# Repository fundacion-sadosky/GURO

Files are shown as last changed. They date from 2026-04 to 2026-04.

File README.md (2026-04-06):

🌐 [English](README.en.md)

# GURO

**Kit de conversión para robots Robobloq Qoopers con [BBC Micro:bit](https://www.microbit.org)**

La Fundación Sadosky desarrolla el kit GURO para actualizar los robots Robobloq Qoopers —ya desplegados en escuelas de todo el país— reemplazando el controlador propietario Qmind Plus por la [BBC Micro:bit](https://www.microbit.org): una placa didáctica de hardware y software completamente abiertos, con una comunidad global activa de millones de docentes y estudiantes.

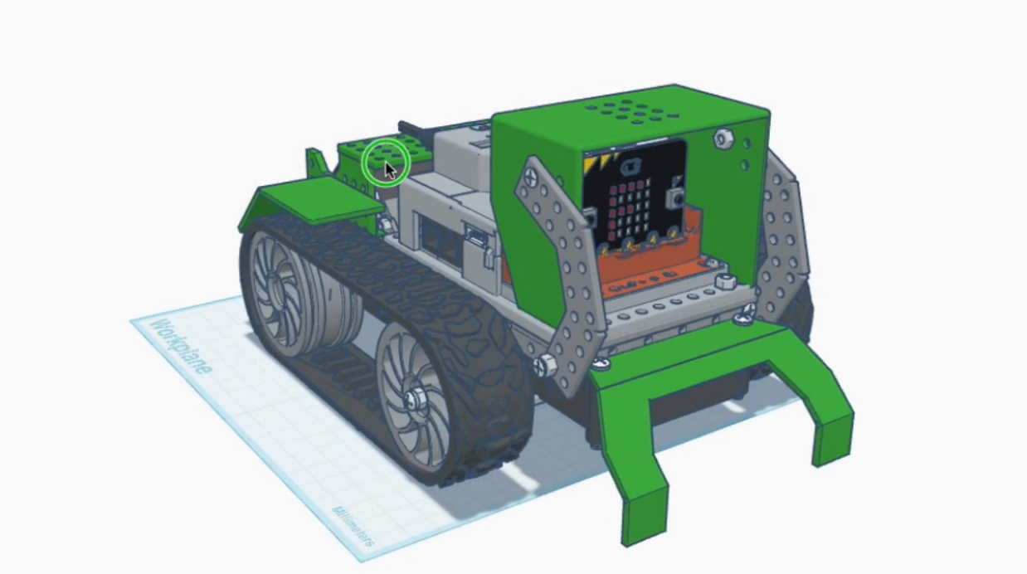
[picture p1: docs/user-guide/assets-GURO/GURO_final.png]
GURO terminado


---

## ¿Qué es el kit GURO?

El kit GURO consiste en una **placa adaptadora** (diseño KiCad incluido en este repositorio) y un **gabinete** que permiten montar una BBC Micro:bit y una placa expansora [Kittenbot Robotbit](https://kittenbothk-eng.readthedocs.io/en/latest/Microbit_eboard/Robotbit/robotbitMC.html) en el chasis del Robobloq Qoopers, conectando los motores y sensores existentes del robot.

El resultado es un robot funcional, programable desde el navegador en bloques visuales o en Python, sin depender de ningún software propietario ni de un único proveedor.

El modelos 3D del robot y el gabinete están disponibles en este repositorio y en [Tinkercad](https://www.tinkercad.com/things/2tzfirybpMV-guro-microrbit-para-robolboq-qoopers-260401)

---

## Requisitos

- **Kit Robobloq Qoopers** — chasis, motores, sensores y partes mecánicas (sin el Qmind Plus)
- **Kit GURO** — placa adaptadora y gabinete Micro:bit (este repositorio)
- **[BBC Micro:bit](https://www.microbit.org)** v1 o v2
- Un destornillador Phillips
- Una computadora con puerto USB

---

## Guía de armado

La documentación completa está publicada en:

**[guro.readthedocs.io](https://guro.readthedocs.io/)**

Incluye el inventario de piezas, 16 pasos ilustrados y las instrucciones de programación. También disponible [en PDF](docs/user-guide_2026-04-01.pdf)

---

## Programación del robot

Una vez armado el GURO, cargá un programa a la Micro:bit desde el navegador, sin instalar nada:

### Opción 1 — Bloques visuales (MakeCode)

Usá el editor [Microsoft MakeCode](https://makecode.microbit.org) con la extensión **Kittenbot Robotbit** para programar el robot con bloques. [Ver instrucciones de la extensión.](https://kittenbothk-eng.readthedocs.io/en/latest/Microbit_eboard/Robotbit/robotbitMC.html)

### Opción 2 — Python

Usá el [editor oficial de MicroPython](https://python.microbit.org/v/3) de la [Micro:bit Educational Foundation](https://github.com/microbit-foundation).

El framework [**microbitML**](https://github.com/fundacion-sadosky/microbitML) (Fundación Sadosky) incluye la actividad `mbGURO`, lista para comandar al robot. Podés descargar el archivo `.hex` y bajarlo directamente a la placa.

---

## Estructura del repositorio

```
docs/               Documentación del sitio (properDocs + Obsidian)
kit GURO/           Inventario del kit 
gabinete/           Gabinete para Micro:bit y placa expansora
placa adaptadora/   Diseño de la placa PCB adaptadora (KiCad)
scripts/            Scripts de generación de documentación (properDocs/MkDocs)
mkdocs.yml          Configuración del sitio de documentación 
docs-requirements.txt  Dependencias Python para compilar la documentación 
```

La carpeta `docs/` está configurada como un vault de [Obsidian](https://obsidian.md), lo que permite editarla sin usar la terminal. Ver [Contribuciones para redactores](https://guro.readthedocs.io/contributing/for-writers/).

---

## Oportunidades de colaboración

Estas son algunas tareas concretas en las que podés contribuir al proyecto:

1. **Avistaje**: si lo usan en tu escuela, compartí la experiencia B)
1. **Completar la Mecánica**: pasar el diseño 3D del gabinete de [Tinkercad](https://www.tinkercad.com/things/2tzfirybpMV-guro-microrbit-para-robolboq-qoopers-260401) a un formato mantenible/paramétrico como openScad.
1. **Completar la Mecánica**: el capó no encaja en la tapa del gabinete.
1. **Completar la Mecánica**: la tapa del gabinete choca con el porta batería del Kittenbot.
1. **Completar la Guía**: los pasos 13, 14 y 16 de la guía de armado no tienen imágenes aún. Si tenés un kit armado, podés tomar las fotos y abrir un PR.
1. **Traducir la documentación al Inglés**: la guía de armado y el README están disponibles solo en español. Traducirlos ampliaría el alcance del proyecto a la comunidad internacional de Micro:bit.
1. **Crear una extensión de MakeCode específica para GURO**: actualmente se usa la extensión genérica de Kittenbot Robotbit. Una extensión propia simplificaría la programación en bloques con nombres y funciones adaptados al GURO.

## Contribuciones

Las contribuciones son bienvenidas, independientemente del perfil técnico.

- **Redactores y docentes**: editá la documentación con [Obsidian](https://obsidian.md) abriendo la carpeta `docs/` como vault. Ver [guía para redactores](https://guro.readthedocs.io/contributing/for-writers/).
- **Desarrolladores**: mirá la [guía para desarrolladores](https://guro.readthedocs.io/contributing/for-developers/).
- **Errores o sugerencias**: abrí un [issue](../../issues) en este repositorio.

---

## Créditos

Colaboradores/as iniciales, por orden alfabético:

| Nombre | Rol |
|---|---|
| Alarcón Lasagno, Ramiro | Doc, SW, HW | 
| Batlle, Leandro | Doc, SW , HW, idea original |
| Gentile Montes, Ezequiel  | Mecánica |
| Medel, Ricardo | Licencias Doc, FLOSS, OSHW  |

*¿Contribuiste al proyecto? Abrí un PR para agregar tu nombre y aportes.*

Este proyecto utiliza la [BBC Micro:bit](https://www.microbit.org), desarrollada por la [Micro:bit Educational Foundation](https://github.com/microbit-foundation). La Micro:bit Foundation publica sus especificaciones de hardware, firmware y recursos educativos bajo licencias abiertas en [github.com/microbit-foundation](https://github.com/microbit-foundation).

---

## Marcas registradas

Los nombres de productos y marcas mencionados en este repositorio (incluyendo BBC Micro:bit, Robobloq, Qoopers, Kittenbot, Robotbit, Microsoft MakeCode, entre otros) son propiedad de sus respectivos titulares y se utilizan únicamente con fines identificativos y descriptivos.

## Naturaleza del proyecto

El desarrollo comenzó en la Fundación Sadosky en el marco del Programa para el Desarrollo de la Infraestructura destinada a Promover la Capacidad Emprendedora financiado por la [CAF | Banco de desarrollo de América Latina y El Caribe](https://www.caf.com/).  GURO es un kit de conversión que permite reutilizar las partes mecánicas, motores y sensores del Robobloq Qoopers con una nueva  placa controladora. El proyecto no modifica ni redistribuye el firmware, software ni diseños de hardware de los productos de terceros que integra. 

## Garantías y responsabilidad

Este proyecto se distribuye sin garantía de ningún tipo, expresa o  implícita. El armado, uso y eventual modificación del kit son responsabilidad exclusiva del usuario. Consultá las licencias GPLv3 y CC BY-SA 4.0 incluidas en este repositorio para los términos  completos. El uso del kit en entornos educativos debe realizarse bajo supervisión docente y conforme a las normativas de seguridad aplicables en cada jurisdicción. 

## Licencias

El proyecto se distribuye bajo una **licencia dual**:

### Código y diseños de hardware
Publicado bajo la [**GNU General Public License v3.0**](LICENSE) (GPLv3).
Podés usar, modificar y redistribuir el código y los diseños KiCad, siempre que cualquier obra derivada se publique bajo la misma licencia.

### Documentación
Publicada bajo [**Creative Commons Atribución-CompartirIgual 4.0 Internacional**](https://creativecommons.org/licenses/by-sa/4.0/) (CC BY-SA 4.0).
Podés copiar, adaptar y redistribuir el contenido —incluso con fines comerciales— siempre que des crédito a los autores originales y distribuyas las obras derivadas bajo la misma licencia.

---

<p align="center">
  <a href="https://www.fundacionsadosky.org.ar">Fundación Sadosky</a>
</p>

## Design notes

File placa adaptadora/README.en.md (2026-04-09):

🌐 [Español](README.md)

# Adapter Board — GURO Kit

[KiCad](https://www.kicad.org/) design of the **adapter board**, a component of the [GURO kit](../kit%20GURO/README.md).

---

## What does this board do?

The adapter board is the central electrical bridge of the GURO kit.
It connects all the peripherals of the Qoopers chassis to the [Kittenbot Robotbit](https://kittenbothk-eng.readthedocs.io/en/latest/Microbit_eboard/Robotbit/robotbitMC.html):

```
Kittenbot Robotbit
      │
      ├── Motors (×2) — 6-pin connectors
      ├── sensors   ─┐
      ├── GPIO       ├── RJ25 connectors (6 Positions / 6 Contacts)
      └── LED panel ─┘
```

It also handles the connection to the kit's **power board**:

> [!WARNING]
> NEVER connect the Robobloq Qoopers battery directly to the Kittenbot Robotbit: the battery voltage must be regulated down to 5V (at 15W), which is the function of the "power board".

---

## PCB design view

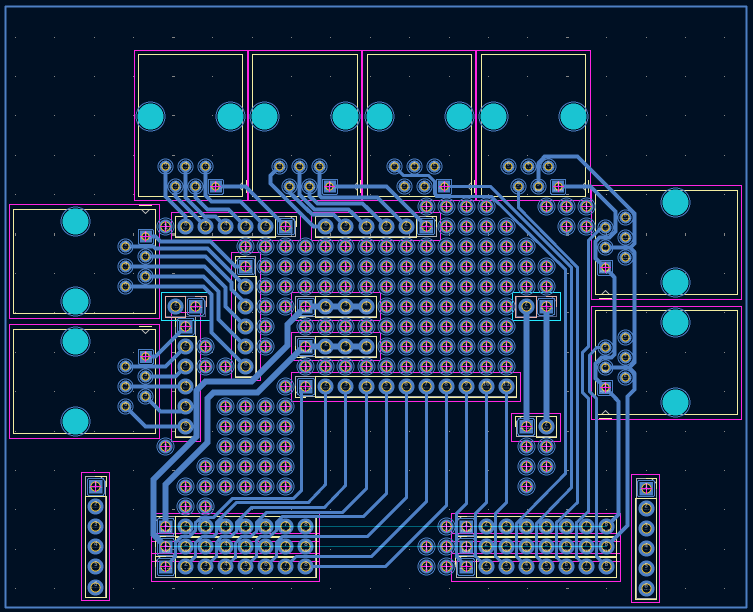
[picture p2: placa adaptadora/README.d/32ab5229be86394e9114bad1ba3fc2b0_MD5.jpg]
KiCad design of the adapter board


The design is optimized to be **interchangeable with a [50×70 mm perfboard](https://www.printables.com/model/797008-perfboard-50x70mm-18-x-24-holes)**, allowing it to be replicated without access to professional PCB manufacturing.

---

## Manufacturing or replacement options

| Option | Difficulty | Result |
|---|---|---|
| **A** — Manufacture from KiCad files | Medium — requires sending Gerbers to a manufacturer | Professional, reproducible PCB |
| **B** — 50×70 mm perfboard | Medium — requires soldering | Equivalent result, no external manufacturer |
| **C** — Direct wiring, no PCB | Low — dupont cables | Functional, less tidy |

All options yield an electrically equivalent result.

---

## Option A — Manufacture from KiCad files

The files in this folder are a [KiCad](https://www.kicad.org/) project (free and open-source PCB design software).

**To manufacture:**
1. Open the project in KiCad and export the **Gerber files** (File → Fabrication Outputs → Gerbers)
2. Upload the Gerbers to any PCB manufacturing service (JLCPCB, PCBWay, Aisler, etc.)
3. Typical order: 5 units, 2 layers, FR4, 1.6 mm thickness

**To edit the design**, you need [KiCad 7 or later](https://www.kicad.org/download/).

---

## Option B — 50×70 mm perfboard

### Components needed for soldering

| Component | Quantity | Notes |
|---|---|---|
| 50×70 mm perfboard | 1 | 2.54 mm pitch |
| Female RJ25 connector (6P6C) | 5 | For sensors and LED panel |
| Male 2-pin connector (2.54 mm pitch) | 2 | For motors |
| Female 40-pin header (2.54 mm pitch) | 2 | For Kittenbot Robotbit |
| Connection wire (wire wrap or similar) | — | For pad bridges |

### General procedure

1. Position the RJ25 connectors using the PCB layout as a reference
2. Solder the connectors and trace the bridges following the KiCad schematic
3. Verify continuity with a multimeter before connecting

---

## Option C — Direct wiring, no PCB

If you have no soldering iron or manufacturer available, it is possible to connect the peripherals directly to the Kittenbot Robotbit using **dupont cables**, without any PCB.

See [step 13 (motors)](../docs/user-guide/index.en.md) and [step 14 (sensors)](../docs/user-guide/index.en.md) of the assembly guide for connection details.

---

## Safety and License

All safety, health, and licensing terms from the [legal section of the main repository](../README.md#guarantees-and-liability) apply here, especially when soldering or handling electrical tools.

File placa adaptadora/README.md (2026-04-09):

🌐 [English](README.en.md)

# Placa Adaptadora — Kit GURO

Diseño [KiCad](https://www.kicad.org/) de la **placa adaptadora**, componente del [kit GURO](../kit%20GURO/README.md).

---

## ¿Qué hace esta placa?

La placa adaptadora es el puente eléctrico central del kit GURO.
Conecta todos los periféricos del chasis Qoopers a la [Kittenbot Robotbit](https://kittenbothk-eng.readthedocs.io/en/latest/Microbit_eboard/Robotbit/robotbitMC.html):

```
Kittenbot Robotbit
      │
      ├── Motores (×2) — conectores de 6 pines
      ├── Sensores  ─┐
      ├── GPIO       ├── conectores RJ25 (6 Posiciones / 6 Contactos)
      └── Panel LED ─┘
```

También incorpora la conexión a la **placa de alimentación** del kit, PRECAUCIÓN:

> [!WARNING]
> NUNCA conectar la batería del Robobloq Qoopers directamente al Kittenbot Robotbit: es necesario regular su tensión a 5V (con 15W), que es la función de la "placa de alimentación".

---

## Vista del diseño PCB

Diseño KiCad de la placa adaptadora

El diseño está optimizado para ser **intercambiable con una [placa universal de 50×70 mm](https://www.printables.com/model/797008-perfboard-50x70mm-18-x-24-holes)**, lo que permite replicarla sin acceso a fabricación de PCB profesional.

---

## Opciones de fabricación o reemplazo

| Opción | Dificultad | Resultado |
|---|---|---|
| **A** — Fabricar con los archivos KiCad | Media — requiere enviar Gerbers a un fabricante | PCB profesional, reproducible |
| **B** — Placa universal 50×70 mm | Media — requiere soldadura | Resultado equivalente, sin fabricante externo |
| **C** — Conexión directa sin PCB | Baja — cables y dupont | Funcional, menos prolijo |

Cualquiera sea la opción elegida, el resultado eléctrico es equivalente.

---

## Opción A — Fabricar con los archivos KiCad

Los archivos de esta carpeta son un proyecto de [KiCad](https://www.kicad.org/) (software libre de diseño de PCB).

**Para fabricar:**
1. Abrí el proyecto en KiCad y exportá los **archivos Gerber** (Archivo → Fabricar → Gerbers)
2. Subí los Gerbers a cualquier servicio de fabricación de PCB (JLCPCB, PCBWay, Aisler, etc.)
3. Pedido típico: 5 unidades, 2 capas, FR4, 1.6 mm de espesor

**Para editar el diseño**, necesitás [KiCad 7 o superior](https://www.kicad.org/download/).

---

## Opción B — Placa universal 50×70 mm

### Componentes necesarios para soldar

| Componente | Cantidad | Notas |
|---|---|---|
| Placa universal perforada 50×70 mm | 1 | Paso de 2.54 mm |
| Conector RJ25 hembra (6P6C) | 5 | Para sensores y panel LED |
| Conector 2 pines macho (paso 2.54 mm) | 2 | Para motores |
| Pin header hembra 40 pines (paso 2.54 mm) | 2 | Para Kittenbot Robotbit |
| Cable de conexión (wire wrap o similar) | — | Para puentes entre pads |

### Procedimiento general

1. Posicioná los conectores RJ25 siguiendo el layout del PCB como referencia
2. Soldá los conectores y trazá los puentes según el esquemático KiCad
3. Verificá continuidad con multímetro antes de conectar

---

## Opción C — Conexión directa sin PCB

Si no disponés de soldador ni fabricante, es posible conectar directamente los periféricos a la Kittenbot Robotbit con **cables dupont**, sin PCB intermedio.

Consultá el [paso 13 (motores)](../docs/user-guide/index.md) y el [paso 14 (sensores)](../docs/user-guide/index.md) de la guía de armado para el detalle de cada conexión.

---

## Precauciones y Licencia

Aplican todas las licencias y precauciones de seguridad y salud citadas en el [apartado legal del repositorio principal](../README.md#garantías-y-responsabilidad), especialmente al realizar soldadura y manipulación de herramientas eléctricas.

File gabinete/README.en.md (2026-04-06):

🌐 [Castellano](README.md)

Case
====

The robot model and the case are available in this repository and on [Tinkercad](https://www.tinkercad.com/things/2tzfirybpMV-guro-microrbit-para-robolboq-qoopers-260401).

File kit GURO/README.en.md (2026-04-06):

🌐 [Castellano](README.md)

# GURO Kit

The GURO kit is the set of parts and documents that allow converting a Robobloq Qoopers robot into a robot with fully open hardware and software, replacing the proprietary Qmind Plus controller with a BBC Micro:bit.

The manufacturing files for all kit parts are available in this repository: the adapter board design in the `placa adaptadora/` folder (KiCad) and the case model in the `gabinete/` folder (STL for 3D printing).

---

## Kit inventory

| Part | Qty. | Notes |
|---|---|---|
| case (base) | 1 | 3D printed. STL file in `gabinete/` |
| case (lid) | 1 | 3D printed. STL file in `gabinete/` |
| Adapter board | 1 | PCB designed in KiCad. Files in `placa adaptadora/` |
| Kittenbot Robotbit board | 1 | Commercial PCB for Micro:bit expansion |
| Power board | 1 | Commercial PCB that regulates voltage from the battery |
| Power cable | 1 | Connects the battery to the power board |

You can build your own kit ("DIY" or "maker") anywhere in the world from this repo's documentation:
1. For the adapter board, there are two options:
   2. Manufacture the PCB from the repo design
   3. Start from a prototype (or "universal") 50×70 mm board and solder the tracks and connectors
2. Print the case (base and lid)
2. Obtain the commercial components: Kittenbot Robotbit and the Power Board

---

## Required components (not included in the kit)

The GURO kit must be combined with the following components, obtained separately:

| Component | Notes |
|---|---|
| BBC Micro:bit v1 or v2 | Main controller board |
| Robobloq Qoopers kit | Does not need to be complete — see the assembly guide |

---

## Assembly guide

The complete step-by-step assembly guide is in the `docs/` folder and accessible at:

**[guro.readthedocs.io](https://guro.readthedocs.io/)**

Also available in PDF at `docs/user-guide_2026-04-01.pdf`.

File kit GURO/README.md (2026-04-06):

🌐 [English](README.en.md)

# Kit GURO

El kit GURO es el conjunto de piezas y documentos, que permiten convertir un robot Robobloq Qoopers en un robot de hardware y software completamente abiertos, reemplazando el controlador propietario Qmind Plus por una BBC Micro:bit.

Los archivos de fabricación de todas las piezas del kit están disponibles en este repositorio: el diseño de la placa adaptadora en la carpeta `placa adaptadora/` (KiCad) y el modelo del gabinete en la carpeta `gabinete/` (STL para impresión 3D).

---

## Inventario del kit

| Pieza | Cant. | Notas |
|---|---|---|
| gabinete (base) | 1 | Impresa en 3D. Archivo STL en `gabinete/` |
| gabinete (tapa) | 1 | Impresa en 3D. Archivo STL en `gabinete/` |
| Placa adaptadora | 1 | PCB diseñada en KiCad. Archivos en `placa adaptadora/` |
| Placa Kittenbot Robotbit | 1 | PCB comercial para expansión de la micro:bit | |
| Placa de alimentación | 1 | PCB comercial que regula la tensión desde la batería | |
| Cable de alimentación | 1 | conecta la batería con la placa de alimentación |

Es posible armar tu propio kit ("DIY" o "maker") en cualquier lugar del mundo, a partir de la documentación de este repo:
1. para la placa adaptadora, hay dos opciones:
   2. fabricar el PCB con el diseño del repo
   3. partir de una placa de prototipado (o "universal") de 50x70 mm, y soldar las pistas y conectores
2. imprimiendo el gabinete (base y tapa)
2. consiguendo los componentes comerciales: Kittenbot Robotbit y Placa de Alimentación

---

## Componentes necesarios (no incluidos en el kit)

El kit GURO debe combinarse con los siguientes componentes, que se consiguen por separado:

| Componente | Notas |
|---|---|
| BBC Micro:bit v1 o v2 | Placa controladora principal |
| Kit Robobloq Qoopers | no es necesario que esté completo, ver la Guía de armado|

---

## Guía de armado

La guía completa de armado paso-a-paso está en la carpeta `docs/` y accesible en:

**[guro.readthedocs.io](https://guro.readthedocs.io/)**

También disponible en PDF en `docs/user-guide_2026-04-01.pdf`.

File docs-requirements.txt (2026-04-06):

properdocs
properdocs[i18n]
mkdocs-static-i18n
mkdocs-material[i18n]
mkdocstrings[python]
mkdocs-gen-files
mkdocs-literate-nav
mkdocs-section-index
mkdocs-obsidian-bridge
mkdocs-autorefs
pymdown-extensions

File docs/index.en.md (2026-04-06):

---
title: Home
---

# GURO

**Conversion kit for Robobloq Qoopers robots with [BBC Micro:bit](https://www.microbit.org)**

Fundación Sadosky develops the GURO kit to upgrade Robobloq Qoopers robots — already deployed in schools across the country — by replacing the proprietary Qmind Plus controller with the [BBC Micro:bit](https://www.microbit.org): an educational board with fully open hardware and software, with an active global community of millions of teachers and students.

GURO assembled

---

## What is the GURO kit?

The GURO kit consists of an **adapter board** and a **case** that allow mounting a BBC Micro:bit and a [Kittenbot Robotbit](https://kittenbothk-eng.readthedocs.io/en/latest/Microbit_eboard/Robotbit/robotbitMC.html) expansion board on the Robobloq Qoopers chassis, connecting the robot's existing motors and sensors.

The result is a functional robot, programmable from the browser using visual blocks or Python, without depending on any proprietary software or a single vendor.

The kit designs and the 3D model of the case are available in the [project repository](https://github.com/fundacion-sadosky/GURO) and on [Tinkercad](https://www.tinkercad.com/things/2tzfirybpMV-guro-microrbit-para-robolboq-qoopers-260401).

---

## Quick access

| I want to… | Go to |
|---|---|
| Assemble the robot | [Getting started](getting-started.md) |
| Read the full assembly guide | [User guide](user-guide/index.md) |
| Contribute to the project | [Contributing](contributing/index.md) |
| View source code and designs | [github.com/fundacion-sadosky/GURO](https://github.com/fundacion-sadosky/GURO) |
| Download the adapter board (KiCad) | [placa adaptadora/](https://github.com/fundacion-sadosky/GURO/tree/main/placa%20adaptadora) |
| Download the case (STL) | [gabinete/](https://github.com/fundacion-sadosky/GURO/tree/main/gabinete) |
| Report a bug or suggest an improvement | [Issues](https://github.com/fundacion-sadosky/GURO/issues) |
| Guide in PDF | [user-guide_2026-04-01.pdf](https://github.com/fundacion-sadosky/GURO/raw/main/docs/user-guide_2026-04-01.pdf) |

---

## Requirements

- **Robobloq Qoopers kit** — chassis, motors, sensors and mechanical parts (without the Qmind Plus)
- **[GURO kit](https://github.com/fundacion-sadosky/GURO/tree/main/kit%20GURO)** — the official one or a handmade assembly
- **[BBC Micro:bit](https://www.microbit.org)** v1 or v2
- A Phillips screwdriver
- A computer with a USB port

---

## Programming the robot

Once the GURO is assembled, load a program onto the Micro:bit from the browser, without installing anything:

**Option 1 — Visual blocks:** use [Microsoft MakeCode](https://makecode.microbit.org) with the **Kittenbot Robotbit** extension.

**Option 2 — Python:** use the [official MicroPython editor](https://python.microbit.org/v/3). The [**microbitML**](https://github.com/fundacion-sadosky/microbitML) framework (Fundación Sadosky) includes the `mbGURO` activity, ready to command the robot.

---

## Repository

The entire project is open code and hardware:

- **Main repository:** [github.com/fundacion-sadosky/GURO](https://github.com/fundacion-sadosky/GURO)
- **Adapter board design (KiCad):** [placa adaptadora/](https://github.com/fundacion-sadosky/GURO/tree/main/placa%20adaptadora)
- **3D model of the case (STL):** [gabinete/](https://github.com/fundacion-sadosky/GURO/tree/main/gabinete)
- **Kit inventory:** [kit GURO/](https://github.com/fundacion-sadosky/GURO/tree/main/kit%20GURO)
- **Issues and suggestions:** [github.com/fundacion-sadosky/GURO/issues](https://github.com/fundacion-sadosky/GURO/issues)
- **Contributing:** [CONTRIBUTING.md](https://github.com/fundacion-sadosky/GURO/blob/main/CONTRIBUTING.md)
- **Code of conduct:** [CODE_OF_CONDUCT.md](https://github.com/fundacion-sadosky/GURO/blob/main/CODE_OF_CONDUCT.md)

The project is distributed under a dual license: **GPLv3** for code and hardware designs, **CC BY-SA 4.0** for documentation.

---

<p align="center">
  <a href="https://www.fundacionsadosky.org.ar">Fundación Sadosky</a>
</p>

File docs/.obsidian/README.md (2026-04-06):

🌐 [English](README.en.md)

PLACEHOLDER FILE

éste repositorio permite editar la la documentación con [Obsidian](https://obsidian.md)

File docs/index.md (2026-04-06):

---
title: Inicio
---

# GURO

**Kit de conversión para robots Robobloq Qoopers con [BBC Micro:bit](https://www.microbit.org)**

La Fundación Sadosky desarrolla el kit GURO para actualizar los robots Robobloq Qoopers —ya desplegados en escuelas de todo el país— reemplazando el controlador propietario Qmind Plus por la [BBC Micro:bit](https://www.microbit.org): una placa didáctica de hardware y software completamente abiertos, con una comunidad global activa de millones de docentes y estudiantes.

GURO terminado

---

## ¿Qué es el kit GURO?

El kit GURO consiste en una **placa adaptadora** y un **gabinete** que permiten montar una BBC Micro:bit y una placa expansora [Kittenbot Robotbit](https://kittenbothk-eng.readthedocs.io/en/latest/Microbit_eboard/Robotbit/robotbitMC.html) en el chasis del Robobloq Qoopers, conectando los motores y sensores existentes del robot.

El resultado es un robot funcional, programable desde el navegador en bloques visuales o en Python, sin depender de ningún software propietario ni de un único proveedor.

Los diseños del kit y el modelo 3D del gabinete están disponibles en el [repositorio del proyecto](https://github.com/fundacion-sadosky/GURO) y en [Tinkercad](https://www.tinkercad.com/things/2tzfirybpMV-guro-microrbit-para-robolboq-qoopers-260401).

---

## Accesos rápidos

| Quiero... | Ir a |
|---|---|
| Armar el robot | [Primeros pasos](getting-started.md) |
| Leer la guía completa de armado | [Guía de usuario](user-guide/index.md) |
| Contribuir al proyecto | [Contribuciones](contributing/index.md) |
| Ver el código fuente y los diseños | [github.com/fundacion-sadosky/GURO](https://github.com/fundacion-sadosky/GURO) |
| Descargar la placa adaptadora (KiCad) | [placa adaptadora/](https://github.com/fundacion-sadosky/GURO/tree/main/placa%20adaptadora) |
| Descargar el gabinete (STL) | [gabinete/](https://github.com/fundacion-sadosky/GURO/tree/main/gabinete) |
| Reportar un error o sugerir una mejora | [Issues](https://github.com/fundacion-sadosky/GURO/issues) |
| Guía en PDF | [user-guide_2026-04-01.pdf](https://github.com/fundacion-sadosky/GURO/raw/main/docs/user-guide_2026-04-01.pdf) |

---

## Requisitos

- **Kit Robobloq Qoopers** — chasis, motores, sensores y partes mecánicas (sin el Qmind Plus)
- **[Kit GURO](https://github.com/fundacion-sadosky/GURO/tree/main/kit%20GURO)** — el oficial o un armado artesanalmente 
- **[BBC Micro:bit](https://www.microbit.org)** v1 o v2
- Un destornillador Phillips
- Una computadora con puerto USB

---

## Programación del robot

Una vez armado el GURO, cargá un programa a la Micro:bit desde el navegador, sin instalar nada:

**Opción 1 — Bloques visuales:** usá [Microsoft MakeCode](https://makecode.microbit.org) con la extensión **Kittenbot Robotbit**.

**Opción 2 — Python:** usá el [editor oficial de MicroPython](https://python.microbit.org/v/3). El framework [**microbitML**](https://github.com/fundacion-sadosky/microbitML) (Fundación Sadosky) incluye la actividad `mbGURO`, lista para comandar al robot.

---

## Repositorio

Todo el proyecto es de código y hardware abiertos:

- **Repositorio principal:** [github.com/fundacion-sadosky/GURO](https://github.com/fundacion-sadosky/GURO)
- **Diseño de la placa adaptadora (KiCad):** [placa adaptadora/](https://github.com/fundacion-sadosky/GURO/tree/main/placa%20adaptadora)
- **Modelo 3D del gabinete (STL):** [gabinete/](https://github.com/fundacion-sadosky/GURO/tree/main/gabinete)
- **Inventario del kit:** [kit GURO/](https://github.com/fundacion-sadosky/GURO/tree/main/kit%20GURO)
- **Issues y sugerencias:** [github.com/fundacion-sadosky/GURO/issues](https://github.com/fundacion-sadosky/GURO/issues)
- **Contribuciones:** [CONTRIBUTING.md](https://github.com/fundacion-sadosky/GURO/blob/main/CONTRIBUTING.md)
- **Código de conducta:** [CODE_OF_CONDUCT.md](https://github.com/fundacion-sadosky/GURO/blob/main/CODE_OF_CONDUCT.md)

El proyecto se distribuye bajo licencia dual: **GPLv3** para código y diseños de hardware, **CC BY-SA 4.0** para documentación.

---

<p align="center">
  <a href="https://www.fundacionsadosky.org.ar">Fundación Sadosky</a>
</p>

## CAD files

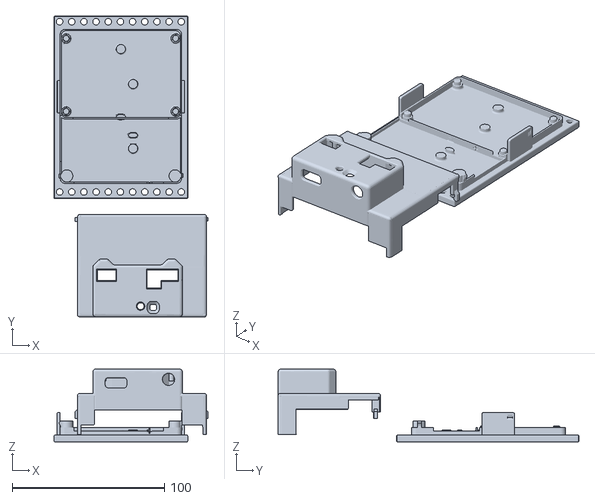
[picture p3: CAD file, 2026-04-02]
gabinete/gabinete.stl
101.3 x 197.9 x 48.0

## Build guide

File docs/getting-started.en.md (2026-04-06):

---
title: Getting started
---

# Getting started

This guide will help you prepare for assembling the GURO robot with the Robobloq Qoopers kit.

## What you need

- GURO kit (micro:bit, adapter boards)
- Robobloq Qoopers kit (all parts included in the box)
- A Phillips screwdriver
- A computer with a USB port (to program the robot)

## Quick start

1. Unpack all components and check the parts list against the inventory
2. Follow the [User guide](user-guide/index.md) for step-by-step assembly instructions
3. Once assembled, connect the robot via USB and load your first program

> [!tip] First time?
> Start with the [User guide](user-guide/index.md) — it walks through each assembly step
> with photos and diagrams.

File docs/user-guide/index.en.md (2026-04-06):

---
title: User guide — GURO Assembly
nro:
---

# GURO — Assembly tutorial

This guide explains, step by step, how to assemble the **Standard** configuration of the **GURO kit**.

The goal is to transform the Robobloq Qoopers robot into a functional robot based on fully open designs.
We will use the [BBC Micro:bit](https://www.microbit.org) as the controller instead of the original Qmind Plus.

GURO assembled

---

## Parts inventory

Before you begin, lay out all parts on a flat surface and check them against the list below.

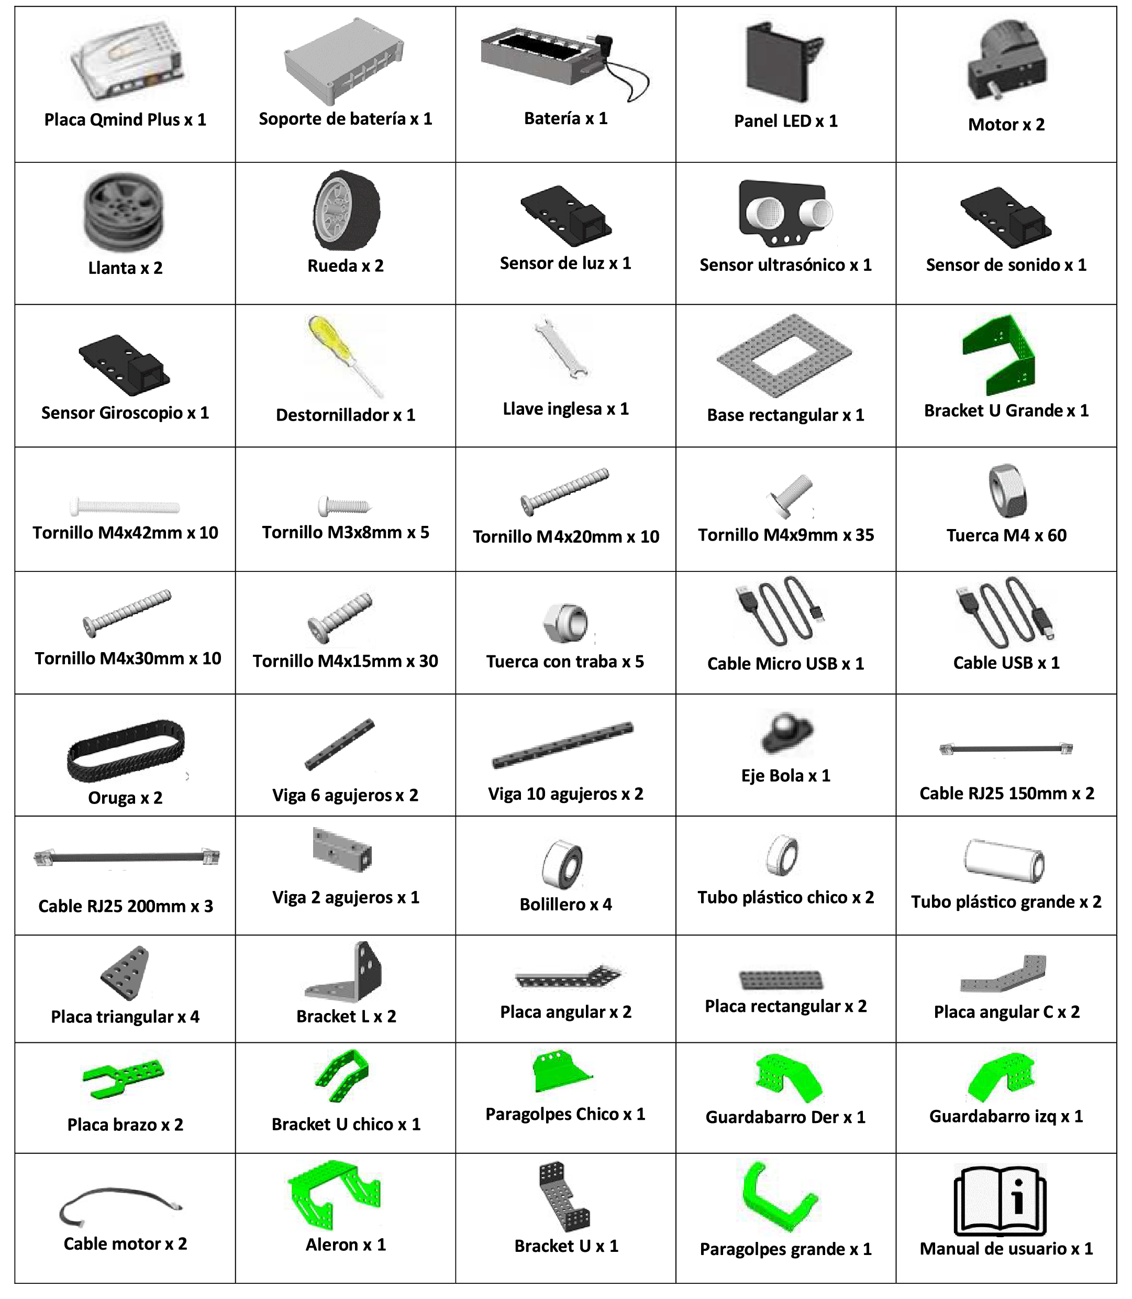
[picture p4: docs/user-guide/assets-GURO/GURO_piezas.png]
Parts list


| Part | Qty. | Part | Qty. |
| --- | --- | --- | --- |
| Qmind Plus board | 1 | Battery holder | 1 |
| Battery | 1 | LED panel | 1 |
| Motor | 2 | Wheel hub | 2 |
| Wheel | 2 | Light sensor | 1 |
| Ultrasonic sensor | 1 | Sound sensor | 1 |
| Gyroscope sensor | 1 | Track | 2 |
| 6-hole beam | 2 | 10-hole beam | 2 |
| 2-hole beam | 1 | Rectangular base | 1 |
| Triangular plate | 4 | Rectangular plate | 2 |
| Angular plate | 2 | Angular plate C | 2 |
| Arm plate | 2 | L-bracket | 2 |
| Large U-bracket | 1 | Small U-bracket | 1 |
| U-bracket | 1 | Ball bearing | 4 |
| Ball axle | 1 | Small plastic tube | 2 |
| Large plastic tube | 2 | Small bumper | 1 |
| Large bumper | 1 | Right mudguard | 1 |
| Left mudguard | 1 | Spoiler | 1 |
| Motor cable | 2 | RJ25 cable 150 mm | 2 |
| RJ25 cable 200 mm | 3 | Micro USB cable | 1 |
| USB cable | 1 | M4×9 mm screw | 35 |
| M4×15 mm screw | 30 | M4×20 mm screw | 10 |
| M4×30 mm screw | 10 | M4×42 mm screw | 10 |
| M3×8 mm screw | 5 | M4 nut | 60 |
| Lock nut | 5 | Screwdriver | 1 |
| Wrench | 1 | User manual | 1 |

> [!note] About the Qmind Plus board
> The Qmind Plus board is **not used** in the GURO kit: it is replaced by the **Micro:bit case**, assembled in Step 11. You may keep it for another project supported by the Robobloq company.

---

## Section 1 — Chassis and motors

### Step 1 — Assemble the chassis frame

**Parts needed:**
- 2 × 10-hole beams
- 1 × 6-hole beam
- 2 × M4×15 mm screws
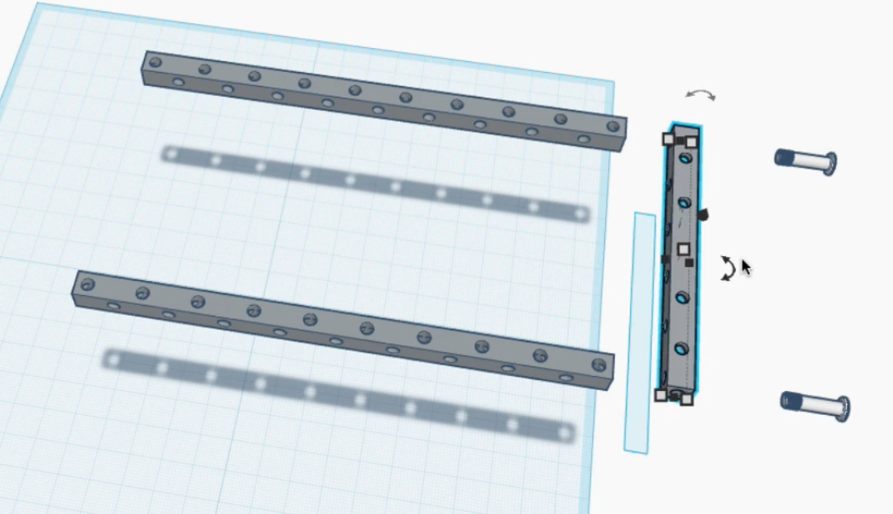
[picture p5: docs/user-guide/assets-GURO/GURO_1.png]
Parts for step 1


Join the two **10-hole beams** in parallel, connecting them at their ends with a **6-hole beam** using M4×15 mm screws. The result is a rectangular frame that forms the base of the chassis.
>[!tip] The holes of the long beams must line up as shown in the diagram

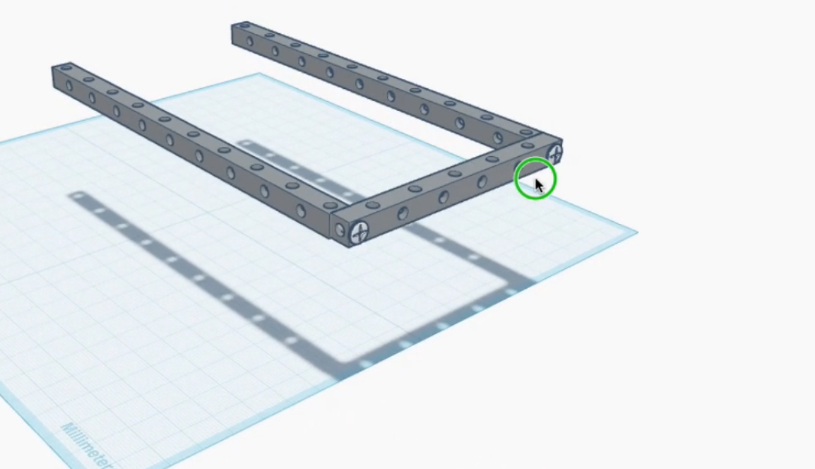
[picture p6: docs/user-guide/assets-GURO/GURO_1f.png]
Result of step 1


---

### Step 2 — Mount the motors (presenting the parts)

**Parts needed:**
- 2 × motors
- 2 × wheel hubs
- 2 × triangular plates
- 4 × M4×15 mm screws and nuts
- 2 × M4×9 mm screws

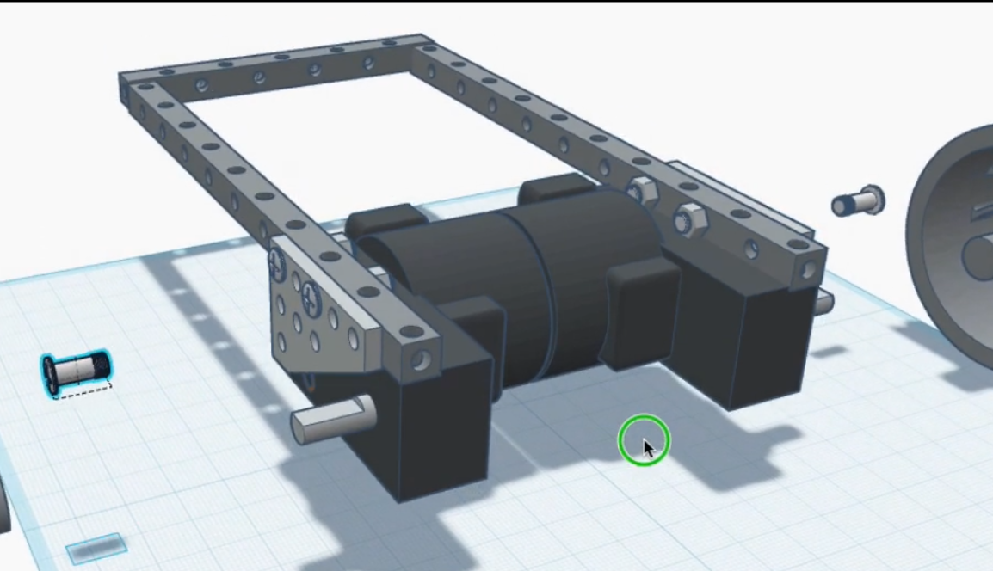
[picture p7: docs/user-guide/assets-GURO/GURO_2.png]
Parts for step 2

Place one **triangular plate** at each free end of a beam, as a bracket, and secure everything with two M4×15 mm screws and nuts (loosely).
Insert the two **motors** inside the rectangular frame, with the output shaft facing outward, and fix them with M4×9 mm screws. See the following detail:

The result is a chassis with the drive motors and main wheels mounted. The screws remain loose and the wheel hubs are not yet fixed. "Presenting the parts."

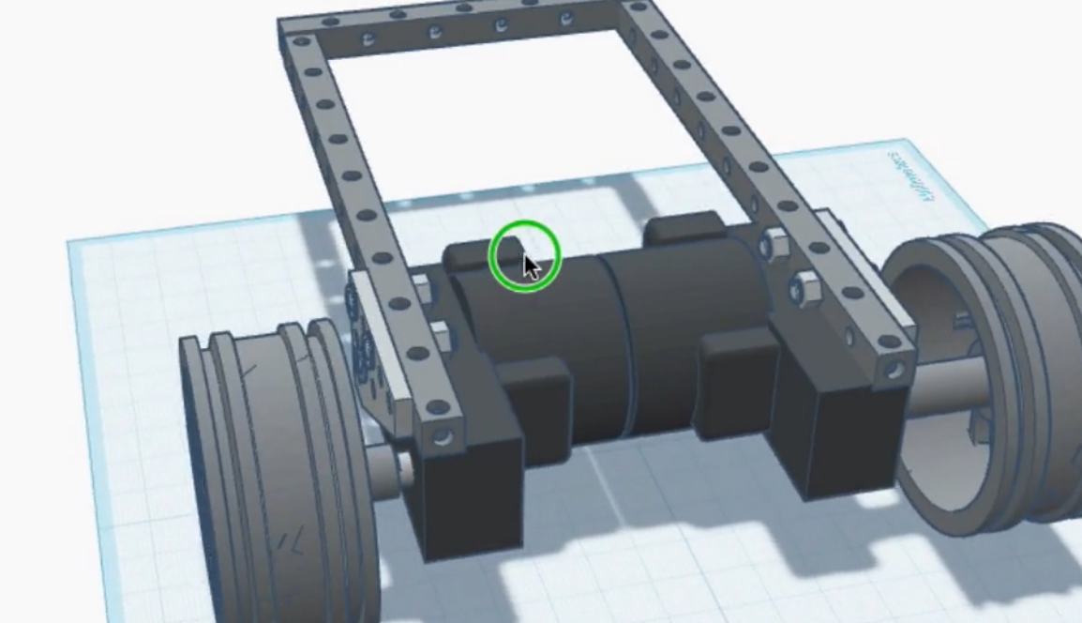
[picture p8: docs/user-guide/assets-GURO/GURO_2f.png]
Result of step 2


---

### Step 3 — Mount the motors (tightening the parts)

**Parts needed:**
- 1 × rectangular plate
- 2 × M4×9 mm screws
- 2 × M3×8 mm screws

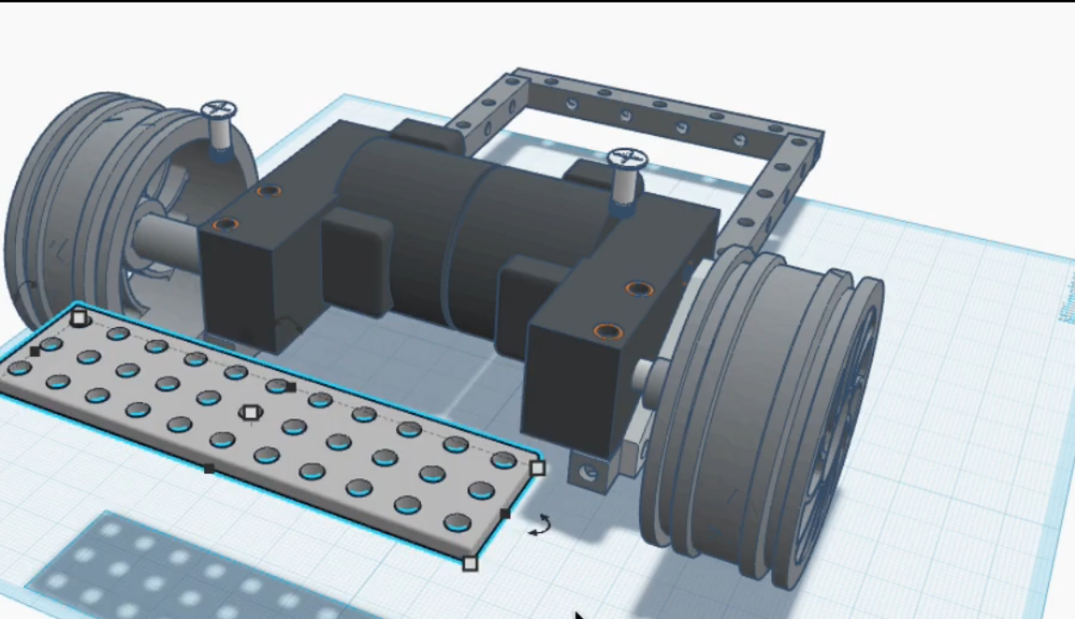
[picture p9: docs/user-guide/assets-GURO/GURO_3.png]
Parts for step 3


Place the **rectangular plate** on the **bottom** face of the motors, aligning the mounting holes with those of the motors (**not** the chassis). Secure it with 2 M4×9 mm screws, tightly. This plate closes the base of the chassis and provides a mounting surface for internal components. Tighten the 6 screws on the triangular plates (from the previous step — if necessary, temporarily remove the wheel hubs). Fix the wheel hubs with M3×8 mm screws.

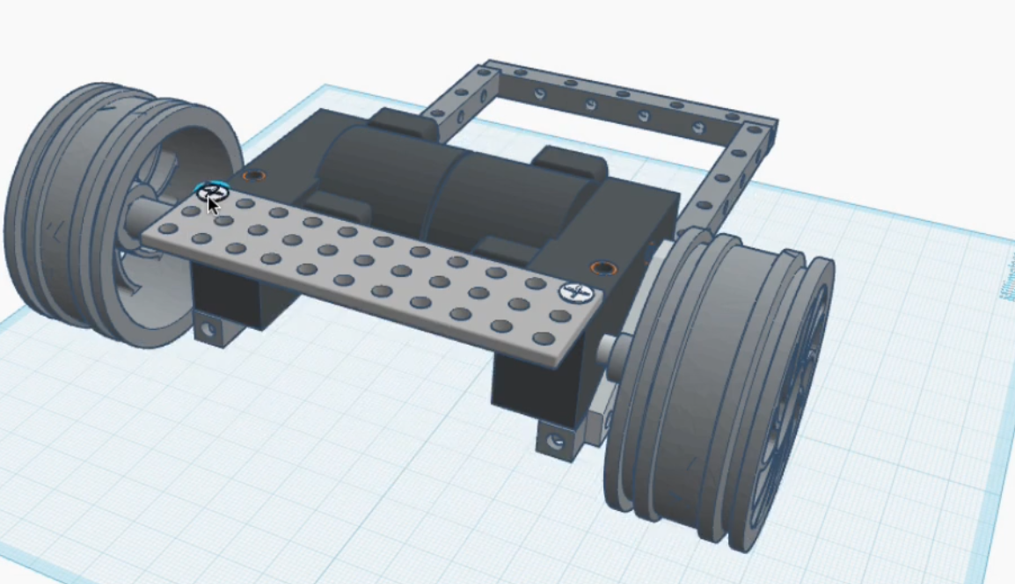
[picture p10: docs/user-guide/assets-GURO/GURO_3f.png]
Result of step 3


---

### Step 4 — Complete the chassis frame

**Parts needed:**
- 1 × U-plate ("U-bracket")
- 4 × M4×15 mm screws and nuts

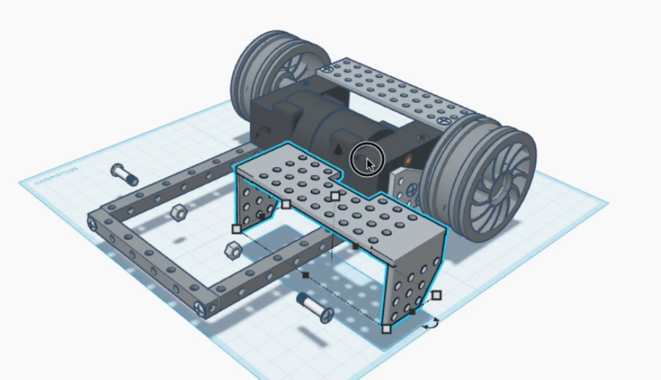
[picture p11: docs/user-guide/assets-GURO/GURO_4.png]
Parts for step 4


Attach the **U-plate** to the chassis, skipping the first hole of each beam, and fixing the plate at the second and third hole of the beam.
The result is the complete lower chassis, robust and ready to receive the running gear.

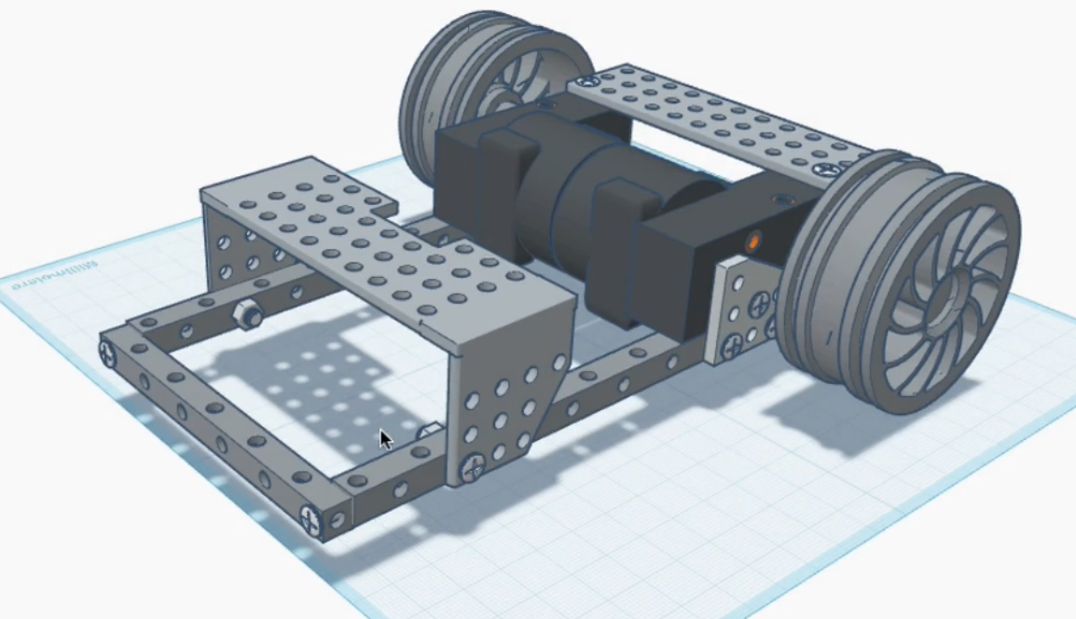
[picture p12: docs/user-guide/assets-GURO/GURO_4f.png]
Result of step 4


---

## Section 2 — Wheels, mudguards and tracks

### Step 5 — Mount the non-drive wheels

**Parts needed:**
- 2 × wheel hubs
- 4 × ball bearings
- 2 × short plastic tubes
- 2 × long plastic tubes (16 mm)
- 2 × M4×42 mm screws
- 2 × M4 lock nuts

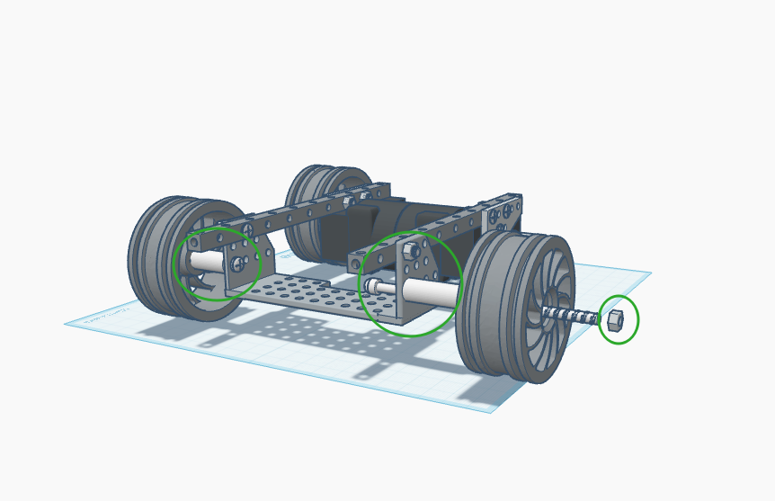
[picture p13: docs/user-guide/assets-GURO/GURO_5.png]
Parts and detail for step 5


Prepare the two remaining wheel hubs as follows: insert two bearings (one on each side) with a small tube in between. The wheel hub looks the same; the bearings do not protrude.

Insert an M4×42 mm screw (the axle) from the inner side of the chassis and a **long plastic tube** from the outer side. Insert the wheel (bearing + hub + spacer + bearing assembly) onto the axle and secure with a **lock nut** (not a standard one). Repeat for the opposite side. These non-drive wheels must spin freely and will guide the tracks.

>[!tip] You can get ahead and do step 10, fitting the tracks to test the tension between the wheels. Stretch each **track** over the complete set of wheels on one side — drive wheel and non-drive wheels — simultaneously, distributing the band evenly around all wheels. Do not force one section at a time. Repeat for the opposite side. Check that the tracks move with minimal effort.

---

### Step 6 — Attach the mudguards

**Parts needed:**
- 2 × mudguards
- 4 × M4×9 mm screws and nuts

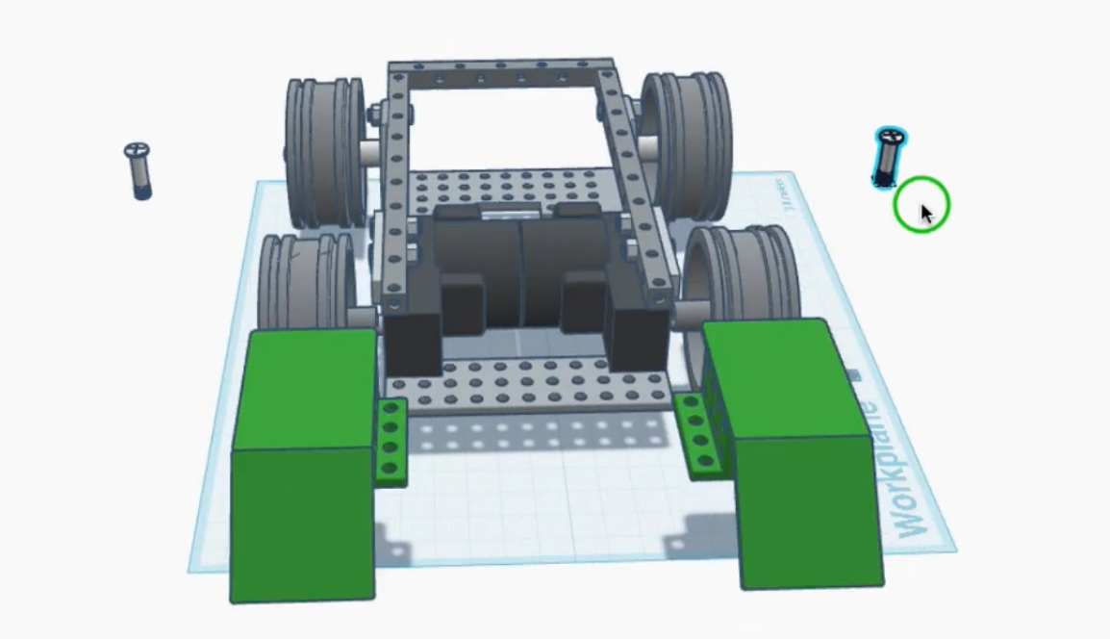
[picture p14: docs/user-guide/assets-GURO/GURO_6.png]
Parts for step 6


Place each **mudguard** on the side of the chassis, at the end of the long beam, over the motor. Secure each one with 2 M4×15 mm screws. Repeat on the other side.
The mudguards protect the GURO from accidental impacts and allow sensors such as the accelerometer, microphone, etc. to be mounted.

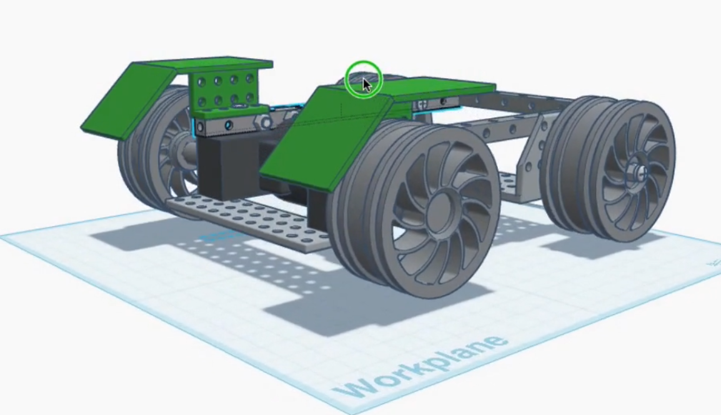
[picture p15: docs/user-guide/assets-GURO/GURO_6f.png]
Result of step 6


---

## Section 3 — Body

### Step 7 — Mount the top platform

**Parts needed:**
- 1 × rectangular base
- M4×15 mm screws

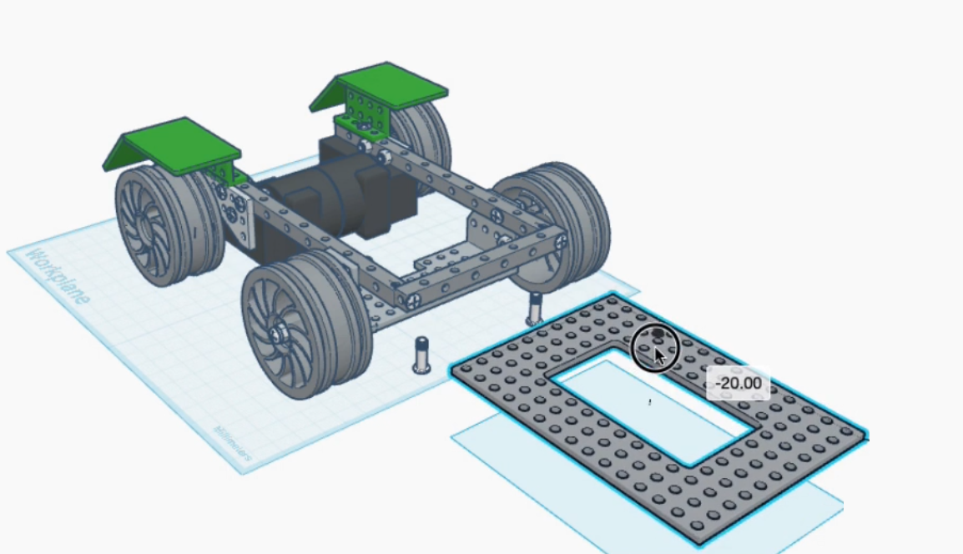
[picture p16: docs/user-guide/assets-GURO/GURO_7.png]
Parts for step 7


Place the **rectangular base** on the side beams of the chassis, aligning its holes with those of the beams, but shifted forward by two rows. Fix it with M4×15 mm screws. Nuts are not required because the **rectangular base** has threaded holes.

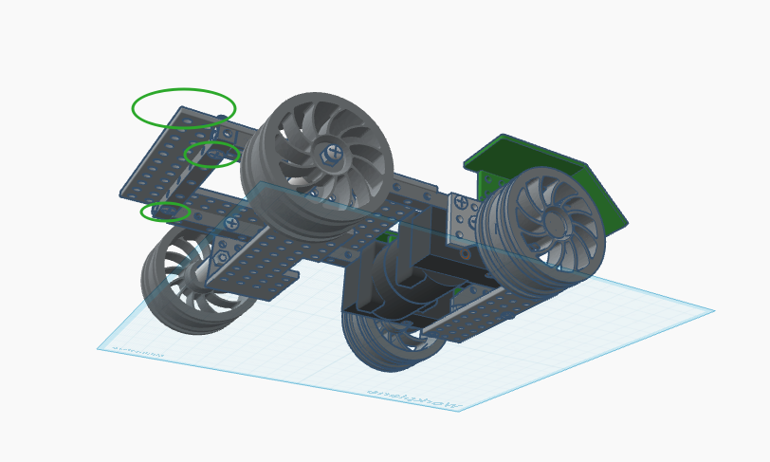
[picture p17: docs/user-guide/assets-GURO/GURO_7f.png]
Result of step 7

This platform is the surface on which all electronic components are mounted, and it is also used to secure the battery underneath (in step 15, which is why it is shifted two rows forward from the chassis).

---

### Step 8 — Install the Micro:bit protection

**Parts needed:**
- 1 × large U-bracket
- 2 × "angular C" plates
- 4 × M4×9 mm screws and nuts

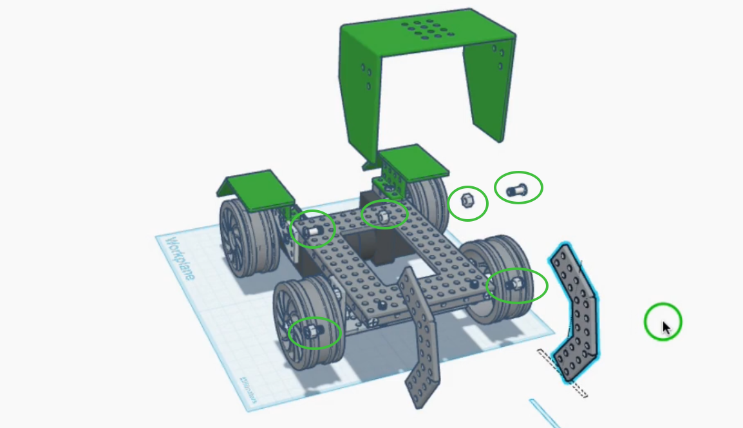
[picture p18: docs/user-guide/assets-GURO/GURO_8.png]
Parts for step 8


Screw one **"angular C" plate** to each side of the **large U-bracket** with M4×9 mm screws and nuts, leaving them loose.
Before screwing the "angular C" plates to the chassis, take two M4×9 mm screws and thread a nut onto each until there is no gap between the nut and the head.
Those nut + screw assemblies will be the pivot of the "angular C" plates — screw them firmly against the chassis (the short beam below the rectangular plate).
Slide the **U-bracket** against the chassis (as in the final figure) and tighten the 4 screws firmly.

The hood protects the Micro:bit case from accidental impacts and can be lifted to access the electronics.

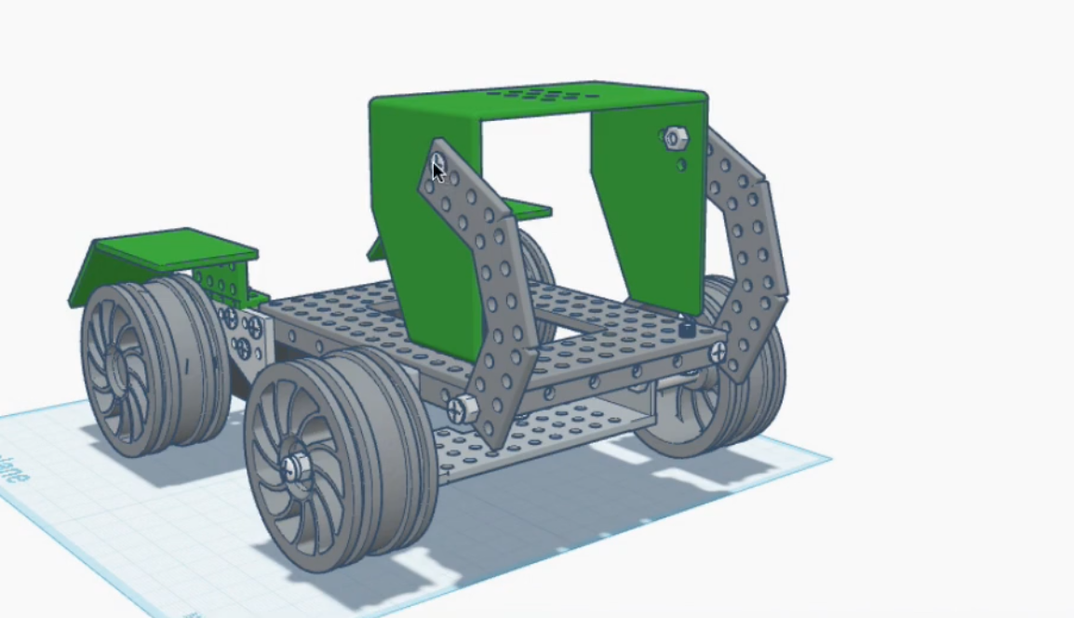
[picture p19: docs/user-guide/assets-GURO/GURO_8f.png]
Result of step 8


---

### Step 9 — Assemble and mount the LED panel bracket

**Parts needed:**
- 1 × LED panel
- 1 × "L-bracket"
- 1 × spoiler
- 3 × M4×15 mm screws and nuts
- 2 × M4×42 mm screws and nuts

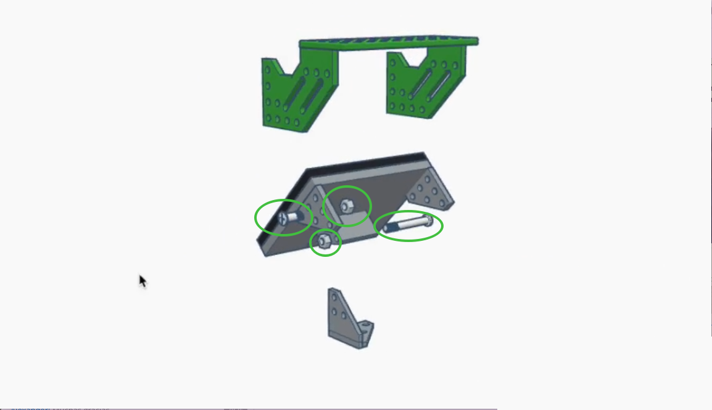
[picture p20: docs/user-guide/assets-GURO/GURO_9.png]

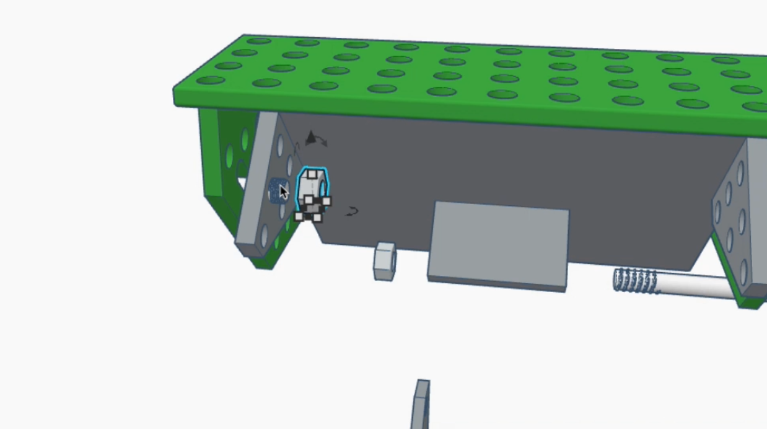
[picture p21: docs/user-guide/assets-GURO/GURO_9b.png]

Join the **spoiler** to the **LED panel** with one M4×15 mm screw on each side. Note the corresponding hole on the panel (shown in grey in the diagram).

The LED panel will be joined to the chassis via the "L-bracket": one M4×42 mm screw with a lock nut on the side of

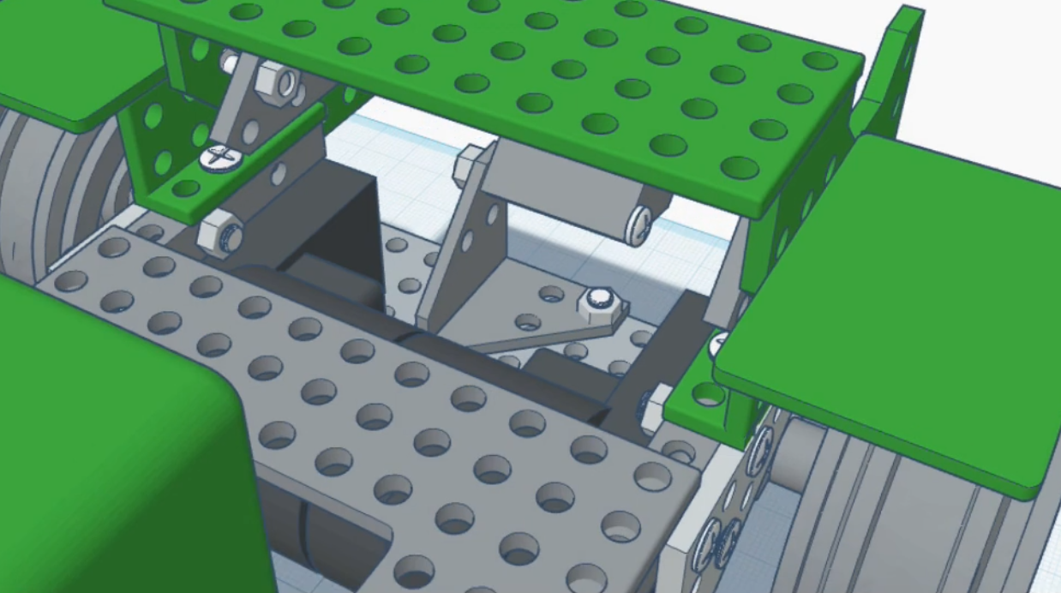
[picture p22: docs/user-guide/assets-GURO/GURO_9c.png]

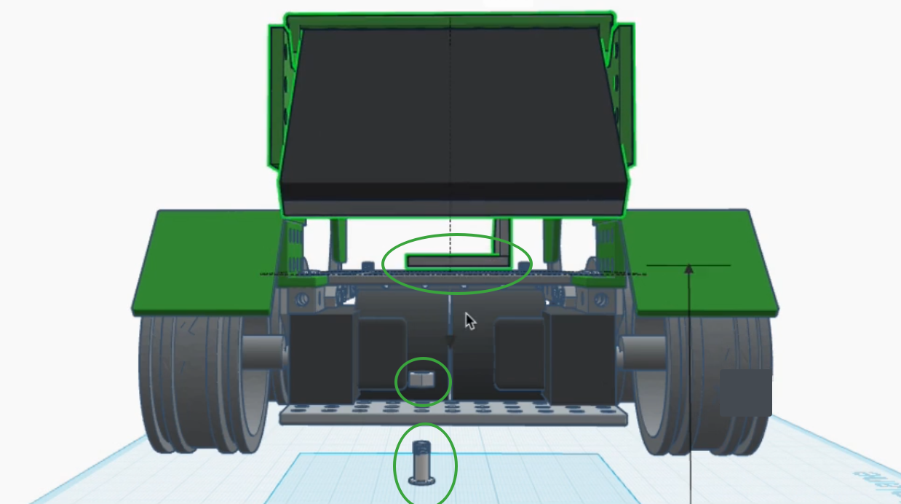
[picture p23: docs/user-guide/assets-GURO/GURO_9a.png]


Secure the complete support at the front of the chassis using the **L-bracket** with one M4×9 mm screw. The LED panel faces forward at a slightly angled position.

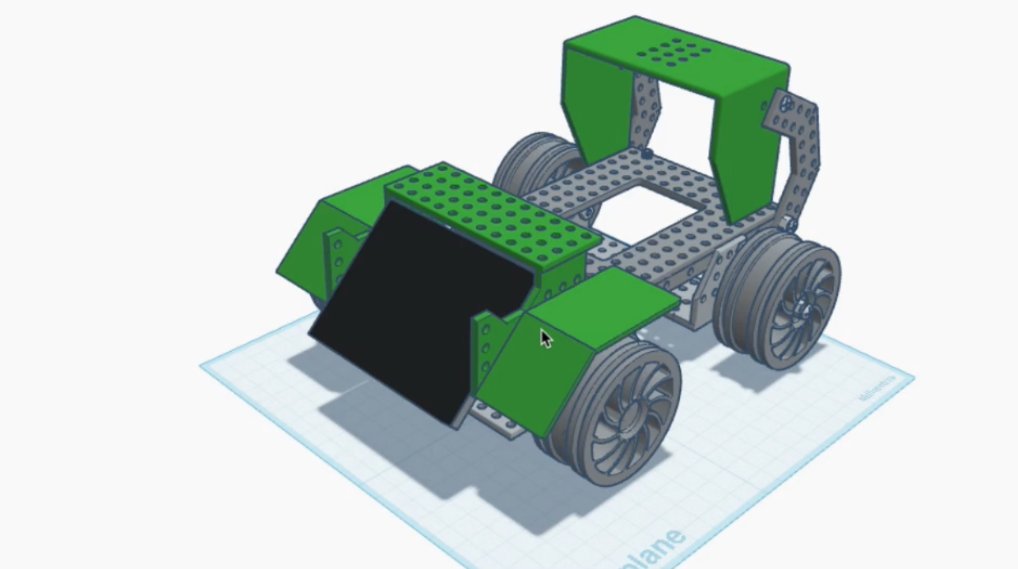
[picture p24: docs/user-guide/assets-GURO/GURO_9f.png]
Result of step 9


> [!tip] LED panel orientation
> The face with the LEDs must be pointing toward the front of the robot. Verify this before tightening the screws definitively.

---

### Step 10 — Attach the tracks

**Parts needed:**
- 2 × tracks (rubber bands)

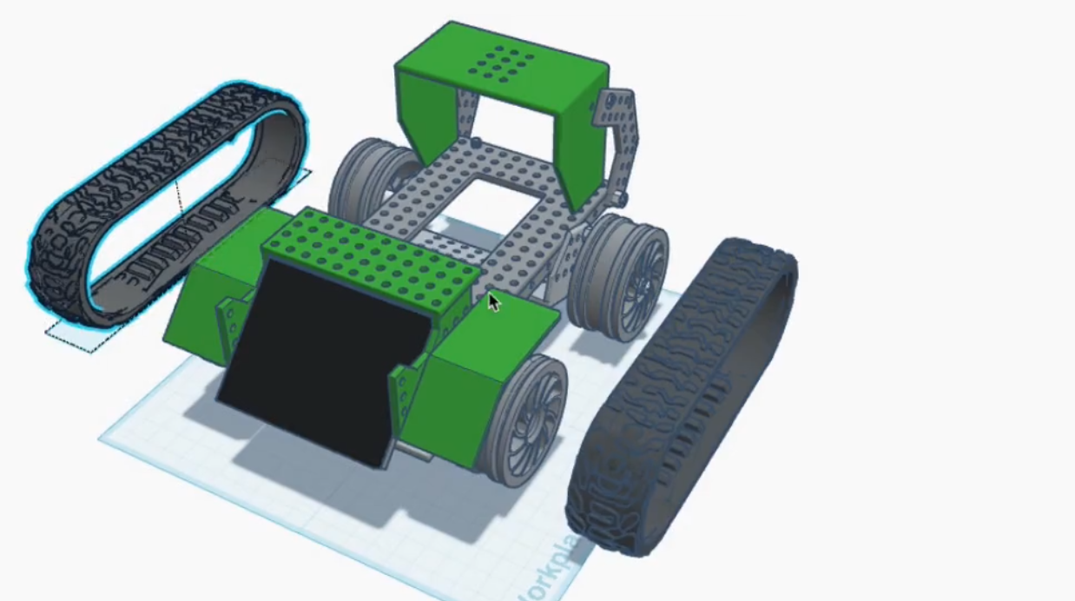
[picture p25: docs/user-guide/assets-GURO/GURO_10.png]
Parts for step 10


Stretch each **track** over the complete set of wheels on one side — drive wheel and idler wheels — simultaneously, distributing the band evenly around all wheels. Do not force one section at a time. Repeat for the opposite side.

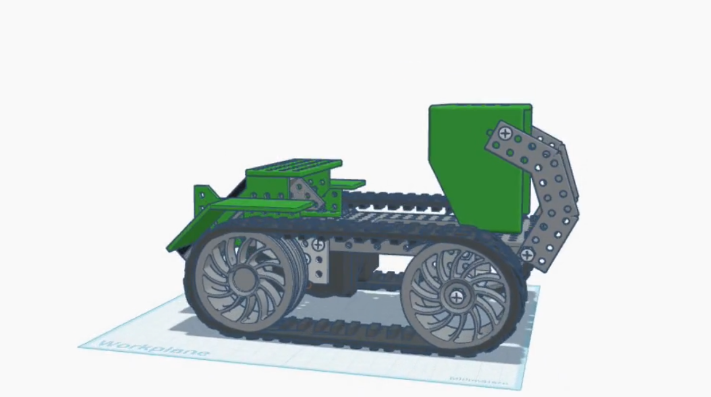
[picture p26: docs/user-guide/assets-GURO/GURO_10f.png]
Result of step 10


> [!tip] Tension check
> Turn each drive wheel by hand. The track should move smoothly, without jumps or folds.

---

## Section 4 — Electronics

### Step 11 — Assemble the Micro:bit case

**Parts needed:**
- 1 × case base board
- 1 × expansion board (carrier board)
- 1 × BBC Micro:bit
- 1 × case lid (grey bracket)
- 4 × M3×8 mm screws

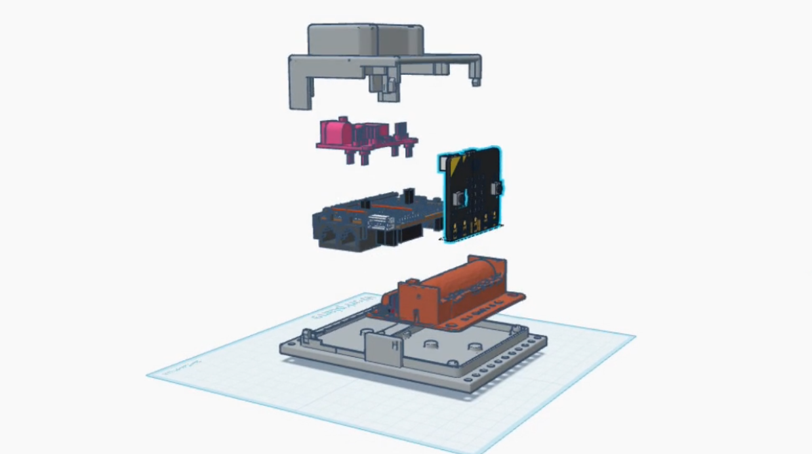
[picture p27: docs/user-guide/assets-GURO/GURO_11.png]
Parts for step 11


Place the **expansion board** on the **base board** and fix it with M3×8 mm screws. Connect the **Micro:bit** to the expansion board by carefully inserting the edge connector (the side with the gold pins) into the corresponding slot. Finally, snap the **lid** onto the assembly to protect the top connections.

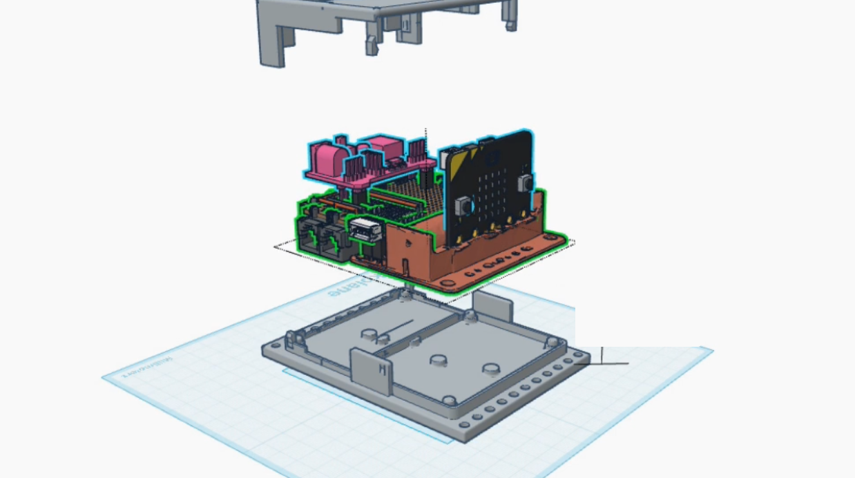
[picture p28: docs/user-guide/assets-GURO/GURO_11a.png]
Assembly detail


The result is the complete **Micro:bit case**: the brain of the GURO, ready to be mounted on the robot.

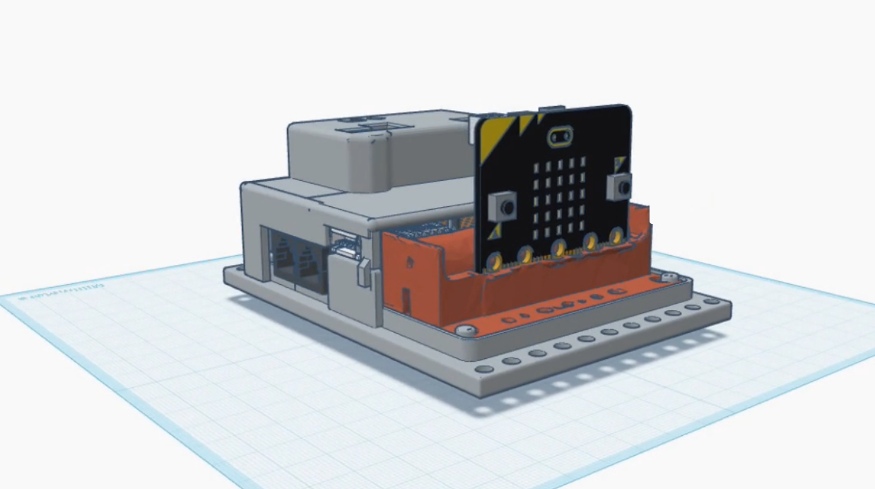
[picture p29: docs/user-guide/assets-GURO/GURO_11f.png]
Result of step 11


> [!note] The Micro:bit replaces the Qmind Plus
> The [BBC Micro:bit](https://www.microbit.org) is a microcontroller with fully open code and hardware, with an active community of millions of users worldwide. It is programmed for free from the browser — without installing any software — using visual blocks or Python. Unlike the Qmind Plus, its specifications are public, its firmware is auditable, and it does not depend on a single vendor for continuity.

---

### Step 12 — Mount the Micro:bit case on the robot

**Parts needed:**
- 1 × Micro:bit case (assembled in the previous step)
- 2 × M4×9 mm screws
- 2 × M4 nuts

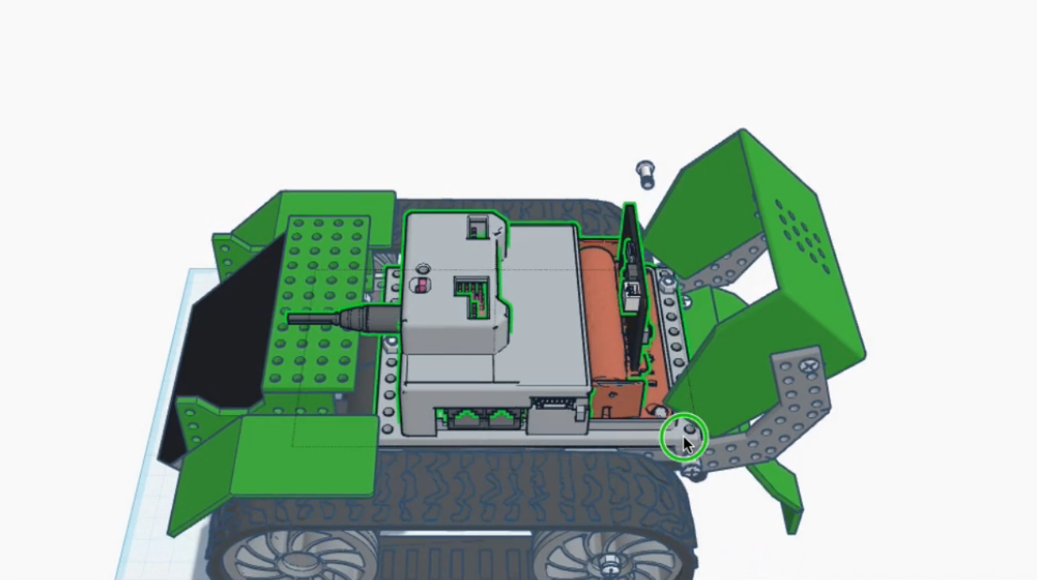
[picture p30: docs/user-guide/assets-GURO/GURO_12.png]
Parts for step 12


With the hood raised, place the **Micro:bit case** on the top platform of the chassis, aligning the holes of the base board with those of the platform. Fix it with 2 M4×9 mm screws and M4 nuts.

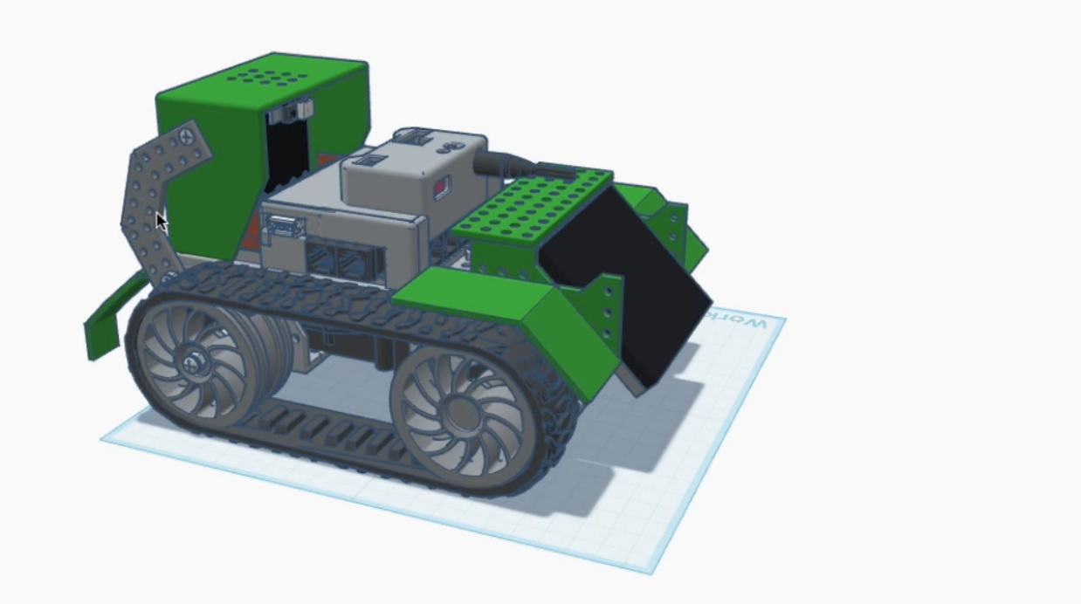
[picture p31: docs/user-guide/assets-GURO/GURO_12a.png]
Detail: positioning


Close the hood. The Micro:bit LED display must be visible through the front opening.

Result of step 12

---

## Section 5 — Wiring and battery

### Step 13 — Connect the motors

> [!warning] Images pending
> Photographs for this step will be published soon.

Connect the **motor cable** of each motor to the corresponding port on the expansion board in the Micro:bit case. The connectors are 2-pin and have a single insertion direction. Each motor has its designated port: left and right.

---

### Step 14 — Connect the sensors

> [!warning] Images pending
> Photographs for this step will be published soon.

Connect each sensor (ultrasonic, light, sound, gyroscope) to its corresponding RJ25 port on the expansion board using the **RJ25 cables**. Use the 150 mm cables for the front sensors and the 200 mm cables for the side or rear sensors.

---

### Step 15 — Install the battery holder and front bumper

**Parts needed:**
- 1 × **battery holder** (without battery)
- 2 × M4×42 mm screws and *lock nuts*
- 1 × large bumper

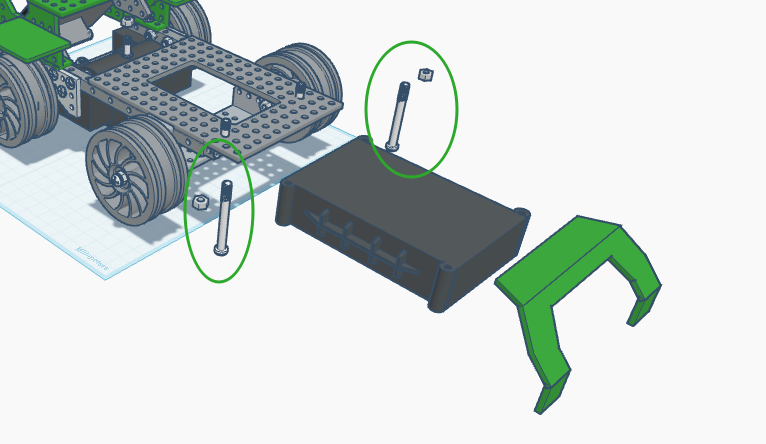
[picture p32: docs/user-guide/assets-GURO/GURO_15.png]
Parts for step 15


Slide the **battery holder** under the chassis, on the side of the non-drive wheels, with the gap facing forward. Secure the holder and the **large bumper** with two M4×42 mm screws and **lock nuts** to the first row of the **rectangular base** installed in step 7.

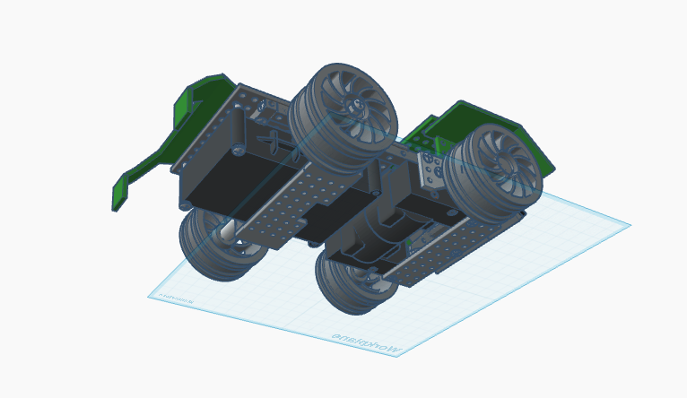
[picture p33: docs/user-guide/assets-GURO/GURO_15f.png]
Result of step 15


---

### Step 16 — Connect the LED panel

> [!warning] Images pending
> Photographs for this step will be published soon.

Connect a **150 mm RJ25 cable** to the rear port of the **LED panel**. Route the cable through the inside of the holder and connect the other end to the designated RJ25 port on the expansion board.

---

## Assembly complete and control software

The GURO is ready. Connect the robot to your computer using the **Micro USB cable** and follow the programming guide to load your first program.

GURO assembled

All done!! Or almost done...

The last touch that brings the GURO robot to life will be loading a program onto the micro:bit. Programming is outside the scope of this document, but there are two convenient options:

1. Program the Micro:bit with blocks in the [MS MakeCode](https://makecode.microbit.org) editor with the [Kittenbot Robotbit](https://kittenbothk-eng.readthedocs.io/en/latest/Microbit_eboard/Robotbit/robotbitMC.html) extension.
2. Program the Micro:bit with real Python using [the official editor](https://python.microbit.org/v/3). The [microbitML framework](https://github.com/fundacion-sadosky/microbitML) includes the `mbGURO` activity ready to command the GURO robot. You can download the .HEX file and upload it to the editor (or flash it directly to the board!).

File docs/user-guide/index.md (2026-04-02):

---
title: Guía de usuario — Armado del GURO
nro:
---

# GURO — Tutorial de armado

Esta guía explica, paso a paso, cómo armar la configuración **Estándar** del **kit GURO**.

El objetivo es transformar el robot Robobloq Qoopers en un robot funcional basado en diseños completamente abiertos. 
Utilizaremos el [BBC Micro:bit](https://www.microbit.org) como controlador en lugar del Qmind Plus original.

GURO terminado

---

## Inventario de piezas

Antes de comenzar, distribuya todas las piezas sobre una superficie plana y verifíquelas contra la lista a continuación.

Lista de piezas

| Pieza | Cant. | Pieza | Cant. |
| --- | --- | --- | --- |
| Placa Qmind Plus | 1 | Soporte de batería | 1 |
| Batería | 1 | Panel LED | 1 |
| Motor | 2 | Llanta | 2 |
| Rueda | 2 | Sensor de luz | 1 |
| Sensor ultrasónico | 1 | Sensor de sonido | 1 |
| Sensor giroscopio | 1 | Oruga | 2 |
| Viga 6 agujeros | 2 | Viga 10 agujeros | 2 |
| Viga 2 agujeros | 1 | Base rectangular | 1 |
| Placa triangular | 4 | Placa rectangular | 2 |
| Placa angular | 2 | Placa angular C | 2 |
| Placa brazo | 2 | Bracket L | 2 |
| Bracket U grande | 1 | Bracket U chico | 1 |
| Bracket U | 1 | Bolillero | 4 |
| Eje bola | 1 | Tubo plástico chico | 2 |
| Tubo plástico grande | 2 | Paragolpes chico | 1 |
| Paragolpes grande | 1 | Guardabarro derecho | 1 |
| Guardabarro izquierdo | 1 | Alerón | 1 |
| Cable motor | 2 | Cable RJ25 150 mm | 2 |
| Cable RJ25 200 mm | 3 | Cable Micro USB | 1 |
| Cable USB | 1 | Tornillo M4×9 mm | 35 |
| Tornillo M4×15 mm | 30 | Tornillo M4×20 mm | 10 |
| Tornillo M4×30 mm | 10 | Tornillo M4×42 mm | 10 |
| Tornillo M3×8 mm | 5 | Tuerca M4 | 60 |
| Tuerca con traba | 5 | Destornillador | 1 |
| Llave inglesa | 1 | Manual de usuario | 1 |

> [!note] Sobre la placa Qmind Plus
> La placa Qmind Plus **no se utiliza** en el kit GURO: es reemplazada por el **gabinete Micro:bit**, que se arma en el Paso 11. Puede reservarla para otro proyecto, que sea soportado por la empresa Robobloq.

---

## Sección 1 — Chasis y motores

### Paso 1 — Armar el marco del chasis

**Piezas necesarias:**
- 2 × viga 10 agujeros
- 1 × viga 6 agujeros
- 2 × tornillo M4×15 mm
Piezas del paso 1

Una las dos **vigas de 10 agujeros** en paralelo, vinculándolas en sus extremos con una **viga de 6 agujeros** mediante tornillos M4×15 mm. El resultado es un marco rectangular que constituye la base del chasis. 
>[!tip] los agujeros de las vigas largas deben quedar como en el diagrama 

Resultado del paso 1

---

### Paso 2 — Montar los motores (presentando las partes)

**Piezas necesarias:**
- 2 × motor 
- 2 x llantas
- 2 × placa triangular
- 4 × tornillo M4×15 mm y sus  tuercas 
- 2 × tornillo M4×9 mm

Piezas del paso 2
Coloque una **placa triangular** por cada extremo libre de una viga, a modo de escuadra y fije todo con dos tornillos M4×15 mm y tuercas (no muy ajustados).
Introduzca los dos **motores** dentro del marco rectangular, con el eje de salida hacia afuera, fíjelos con tornillos M4x9 mm. Vea el siguiente detalle:

El resultado es un chasis con los motores de tracción y las ruedas principales montadas. Los tornilos se mantienen flojos, y las llantas sin fijación. "Presentamos las piezas"

Resultado del paso 2

---

### Paso 3 — Montar los motores (ajustando las partes)

**Piezas necesarias:**
- 1 × placa rectangular
- 2 × tornillo M4×9 mm
- 2 x tornillo M3x8 mm

Piezas del paso 3

Apoye la **placa rectangular** sobre la cara **inferior** de los motores alineando los agujeros de fijación con los de los motores (**no** los del chassis). Asegúrela con 2 tornillos M4×9 mm, fuertemente apretados. Esta placa cierra la base del chasis y provee superficie de montaje para los componentes internos. Apriete los 6 tornillos de las placas triangulares (paso anterior, si es necesario saque las llantas momentáneamente). Fije las llantas con tornillos M3x8 mm

Resultado del paso 3

---

### Paso 4 — Completar el marco del chasis

**Piezas necesarias:**
- 1 × placa en U ("Braket U")
- 4 x tornillos M4×15 mm y sus tuercas

Piezas del paso 4

Incorpore la **placa en U**** al chasis, salteanto el primer agujero de cada viga, fijando la placa con en el segundo y tercer agujero de la viga.
El resultado es el chasis inferior completo, robusto y listo para recibir el tren de rodaje.

Resultado del paso 4

---

## Sección 2 — Ruedas, guardabarros y orugas

### Paso 5 — Montar las ruedas sin tracción

**Piezas necesarias:**
- 2 × llanta
- 4 ×  Rodamientos (conocidos como Bolilleros o Rulemanes)
- 2 × tubo plástico corto 
- 2 × tubo plástico largo (16 mm)
- 2 x tornillo M4x42mm
- 2 × tuerca con traba M4

Piezas y detalle del paso 5

Prepare las dos llantas restantes de la siguiente manera: introduzca dos rodamientos (uno de cada lado), conun tubo chico entre medio. La llanta queda con el mismo aspecto, los rodamientos no sobresalen.

Inserte  un tornillo de M4x42 mm  (el eje) por el lado interno del chasis y  **tubo plástico largo**  por el lado externo. Inserte la rueda (conjunto rueda+rodamiento+separador+rodamiento)  en el eje y asegure con una **tuerca con traba** (no de las comunes). Repita para el lado opuesto. Estas ruedas no-motrices  deben girar libremente y guiarán las orugas.

 >[!tip] Es posible adelantar el paso 10, colocando las orugas para probar la tensión entre las ruedas. Estire cada **oruga** sobre el conjunto completo de ruedas de un mismo lateral —rueda motriz y ruedas no-motrices— de manera simultánea, distribuyendo la banda de forma pareja alrededor de todas las ruedas. No fuerce un sector a la vez. Repita para el lateral opuesto. Pruebe que las orugas se mueven con un esfuerzo mínimo.

---

### Paso 6 — Colocar los guardabarros

**Piezas necesarias:**
- 2 × guardabarro
- 4 × tornillo M4×9 mm y sus tuercas

Piezas del paso 6

Coloque en **guardabarro** sobre el lateral del chasis, al final de la vila larga, sobre el motor. Fije cada con 2 tornillos M4×15 mm. Repita en el otro costado.
Los guardabarros otorgan a GURO protección frente a impactos y permiten colocar sensores como acelerómetro, micrófono, etc.

Resultado del paso 6

---

## Sección 3 — Carrocería

### Paso 7 — Montar la plataforma superior

**Piezas necesarias:**
- 1 × base rectangular 
- tornillos M4×15 mm

Piezas del paso 7

Apoye la **base rectangular** sobre las vigas laterales del chasis, alineando sus agujeros con los de las vigas, pero adelantada dos filas. Fíjela con tornillos M4×15 mm. No son necesarias tuercas, ya que la **base rectangular** presenta  agujeros roscados. 

Resultado del paso 7
Esta plataforma es la superficie sobre la que se montan todos los componentes electrónicos, y para fijar la batería debajo (en el paso 15, por eso las dos filas adelantadas al chasis)

---

### Paso 8 — Instalar la protección del Micro:bit

**Piezas necesarias:**
- 1 × "bracket U" grande
- 2 × placa "angular C"
- 4 x tornillos M4×9 mm y sus tuercas

Piezas del paso 8

Atornille a cada costado del **"bracket U" grande**, un placa "angular C", con tornillos M4×9 mm y sus tuercas, dejándolas flojas.
Antes de atornillar las placas "angular C" al chasis, tome dos tornillos M4x9 mm y rosque a cada una, una tuerca hasta hasta que no que luz entre la tuerca y la cabeza. 
Esos ensambles tuerca+tornillo será el eje de las "angular C", atorníllelos fuertemente contra el chasos (la viga corta bajo la placa rectangular.)
Desplaze el  **"bracket U"** contra el chasis (como en la figura final) y ajuste fuertemente los 4 tornillos.

El capó protege el gabinete Micro:bit de golpes accidentales y se levantar para acceder a la electrónica.

Resultado del paso 8

---

### Paso 9 — Armar y montar el soporte del panel LED

**Piezas necesarias:**
- 1 × panel LED
- 1 × "Braket L"
- 1 × Alerón
- 3 x tornillos M4×15 mm y sus tuercas
- 2 x tornillos M4×42 mm y sus tuerca

Piezas del paso 9
Piezas del paso 9
Una el **alerón** al **panel LED** con un tornillo de M4×15 mm por cada lado. Observe el agujero correspondiente del panel (gris el esquema)

La panel LED se unirá con el chasis por medio del "Braket L": un tornillo M4x42 mm con tureca con traba de lado de

Detalle: inserción del bolillero
Detalle: inserción del bolillero

Fije el soporte completo en la parte delantera del chasis mediante el **bracket L** con un tornillo M4×9 mm. El panel LED queda orientado hacia el frente en posición levemente inclinada.

Resultado del paso 9

> [!tip] Orientación del panel LED
> La cara con los LEDs debe quedar mirando hacia adelante del robot. Verifique esto antes de apretar los tornillos definitivamente.

---

### Paso 10 — Colocar las orugas

**Piezas necesarias:**
- 2 × oruga (banda de goma)

Piezas del paso 10

Estire cada **oruga** sobre el conjunto completo de ruedas de un mismo lateral —rueda motriz y ruedas locas— de manera simultánea, distribuyendo la banda de forma pareja alrededor de todas las ruedas. No fuerce un sector a la vez. Repita para el lateral opuesto.

Resultado del paso 10

> [!tip] Verificación de tensión
>  gire cada rueda motriz a mano. La oruga debe moverse con fluidez, sin saltos ni pliegues.

---

## Sección 4 — Electrónica

### Paso 11 — Armar el gabinete Micro:bit

**Piezas necesarias:**
- 1 × placa base del gabinete
- 1 × placa expansora (carrier board)
- 1 × BBC Micro:bit
- 1 × tapa del gabinete (bracket gris)
- 4 × tornillo M3×8 mm

Piezas del paso 11

Coloque la **placa expansora** sobre la **placa base** y fíjela con tornillos M3×8 mm. Conecte el **Micro:bit** a la placa expansora encajando con cuidado el conector de borde (el lado de los pines dorados) en la ranura correspondiente. Por último, encaje la **tapa** sobre el conjunto para proteger las conexiones superiores.

Detalle de ensamblado

El resultado es el **gabinete Micro:bit** completo: el cerebro del GURO, listo para ser montado en el robot.

Resultado del paso 11

> [!note] El Micro:bit reemplaza al Qmind Plus
> El [BBC Micro:bit](https://www.microbit.org) es un microcontrolador de código y hardware completamente abiertos, con una comunidad activa de millones de usuarios en todo el mundo. Se programa de forma gratuita desde el navegador —sin instalar ningún software— en bloques visuales o en Python. A diferencia del Qmind Plus, sus especificaciones son públicas, su firmware es auditable y no depende de un único proveedor para su continuidad.

---

### Paso 12 — Montar el gabinete Micro:bit en el robot

**Piezas necesarias:**
- 1 × gabinete Micro:bit (ensamblado en el paso anterior)
- 2 × tornillo M4×9 mm
- 2 × tuerca M4

Piezas del paso 12

Con el capó levantado, coloque el **gabinete Micro:bit** sobre la plataforma superior del chasis, alineando los agujeros de la placa base con los de la plataforma. Fíjelo con 2 tornillos M4×9 mm y tuercas M4.

Detalle: posicionamiento

Cierre el capó. La pantalla de LEDs del Micro:bit debe quedar visible a través de la abertura delantera.

Resultado del paso 12

---

## Sección 5 — Cableado y batería

### Paso 13 — Conectar los motores

> [!warning] Imágenes pendientes
> Las fotografías de este paso se publicarán próximamente.

Conecte el **cable motor** de cada motor al puerto correspondiente en la placa expansora del gabinete Micro:bit. Los conectores son de 2 pines y tienen un sentido único de inserción. Cada motor cuenta con su puerto designado: izquierdo y derecho.

---

### Paso 14 — Conectar los sensores

> [!warning] Imágenes pendientes
> Las fotografías de este paso se publicarán próximamente.

Conecte cada sensor (ultrasónico, de luz, de sonido, giroscopio) a su puerto RJ25 correspondiente en la placa expansora mediante los **cables RJ25**. Utilice los cables de 150 mm para los sensores delanteros y los de 200 mm para los sensores laterales o traseros.

---

### Paso 15 — Instalar el soporte de batería y el paragolpes delantero

**Piezas necesarias:**
- 1 × **soporte de batería** (sin batería)
- 2 × tornillos M4×42 mm y sus *tuercas con traba*
- 1 x paragolpes grande

Piezas del paso 15

Deslice el **soporte de batería** debajo del chasis, del lado de las ruedas no-tractoras, con el hueco para el frente. Asegure el soporte y el **paragolpes grande** con un dos tornillos M4×42 mm y sus **tuercas con traba** a la primera fila de la **base rectangular** instalada en el paso 7.

Resultado del paso 15

---

### Paso 16 — Conectar el panel LED

> [!warning] Imágenes pendientes
> Las fotografías de este paso se publicarán próximamente.

Conecte un **cable RJ25 de 150 mm** al puerto trasero del **panel LED**. Pase el cable por el interior del soporte y conecte el otro extremo al puerto RJ25 designado en la placa expansora.

---

## Armado completo y software de control

El GURO está listo. Conecte el robot a su computadora mediante el **cable Micro USB** y siga la guía de programación para cargar el primer programa.

GURO terminado

Listo listo!! O casi listo... 

 El último toque que dé vida al robot GURO,  será cargarle un programa a la micro:bit. La programación cae fuera de éste documento, pero hay dos opciones convenientes:
 
1. Programar la Microbit  con bloques en el editor de [MS Makecode](https://makecode.microbit.org) con la extensión de [Kittenbot Robotbit](https://kittenbothk-eng.readthedocs.io/en/latest/Microbit_eboard/Robotbit/robotbitMC.html)   
2. Programar la Microbit con verdadero Python desde [el editor oficial](https://python.microbit.org/v/3).  El [framework microbitML](https://github.com/fundacion-sadosky/microbitML) cuenta con  la actividad `mbGURO` lista para comandar al robot GURO. Puede  descargar el archivo .HEX y subirlo al editor (o bajarlo directamente a la placa!)

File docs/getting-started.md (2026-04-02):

---
title: Primeros pasos
---

# Primeros pasos

Esta guía te ayuda a prepararte para el armado del robot GURO con el kit Robobloq Qoopers.

## Qué necesitás

- Kit GURO (micro:bit, placas adaptadoras)
- Kit Robobloq Qoopers (todas las piezas incluidas en la caja)
- Un destornillador Phillips
- Una computadora con puerto USB (para programar el robot)

## Inicio rápido

1. Desembalá todos los componentes y verificá la lista de piezas contra el inventario
2. Seguí la [Guía de usuario](user-guide/index.md) para las instrucciones de armado paso a paso
3. Una vez armado, conectá el robot por USB y cargá tu primer programa

> [!tip] ¿Primera vez?
> Comenzá con la [Guía de usuario](user-guide/index.md) — recorre cada paso del armado
> con fotos y diagramas.

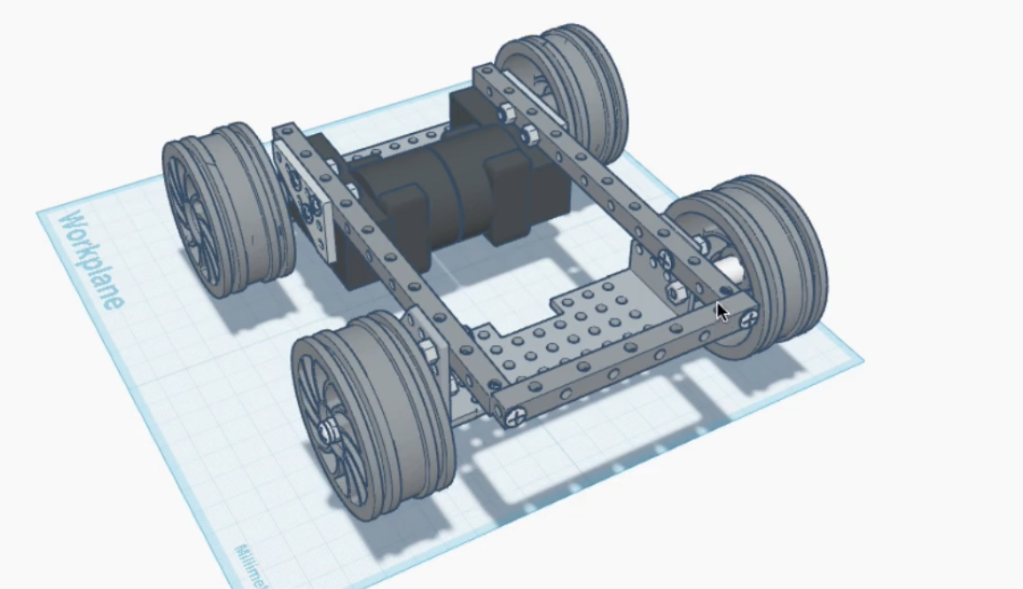
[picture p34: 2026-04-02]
docs/user-guide/assets-GURO/GURO_5f.png

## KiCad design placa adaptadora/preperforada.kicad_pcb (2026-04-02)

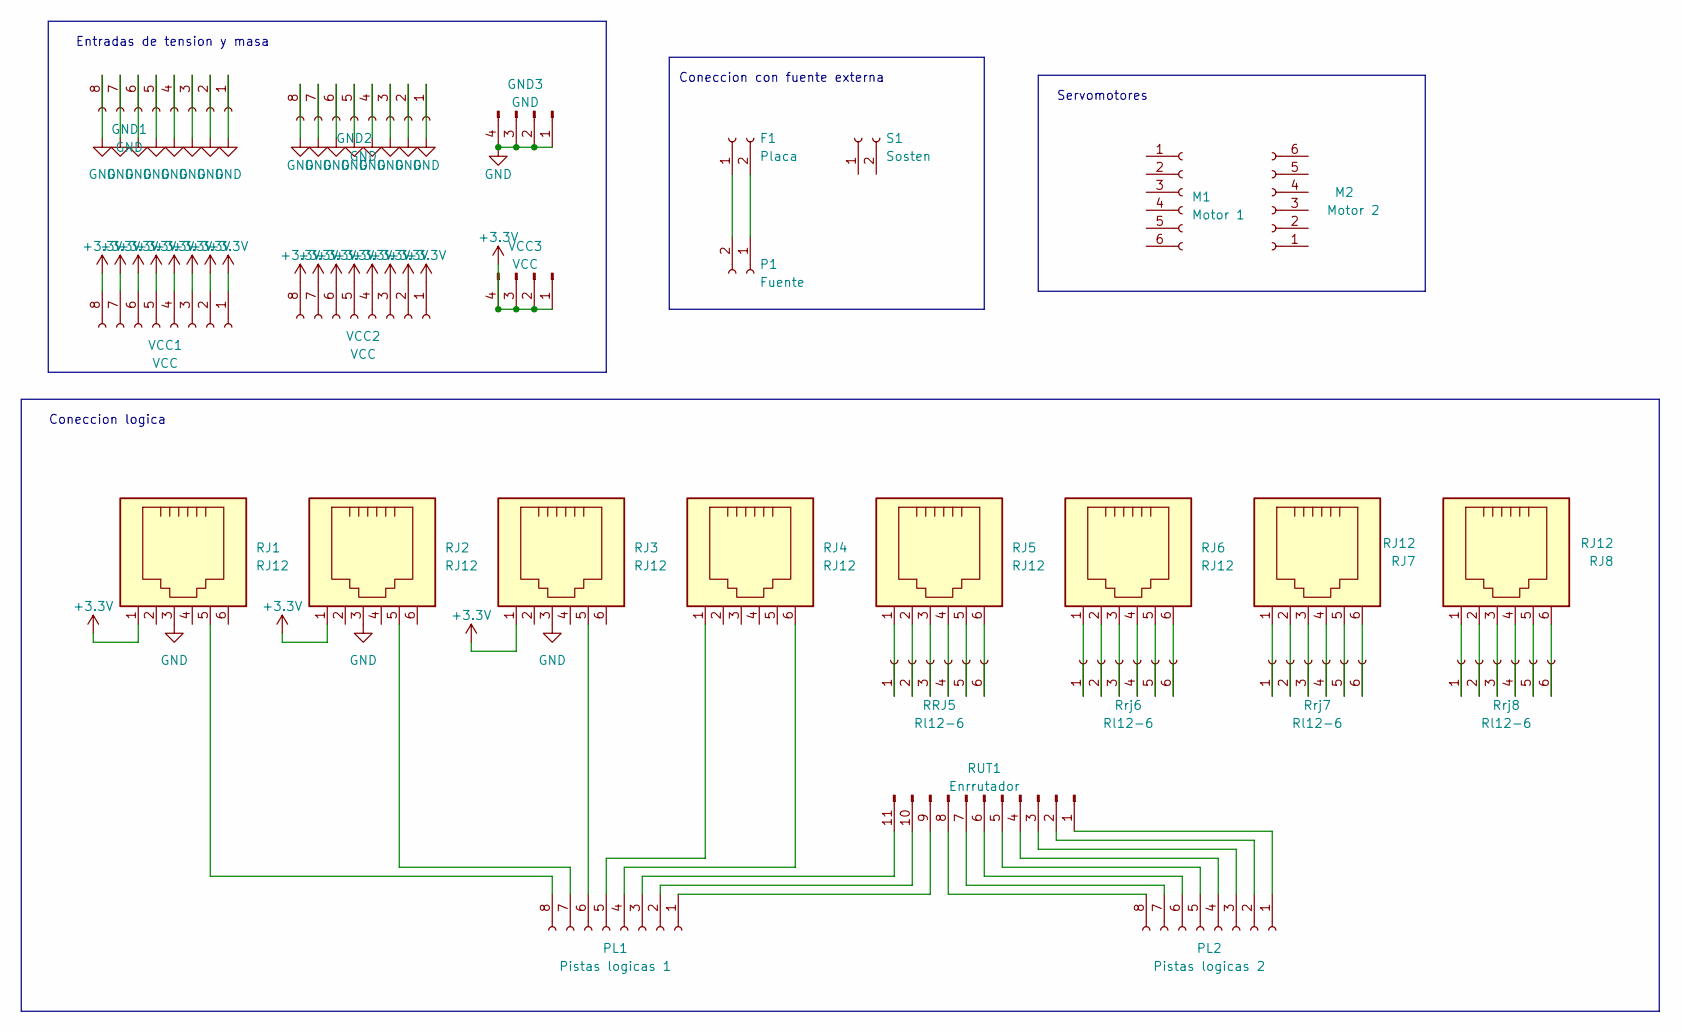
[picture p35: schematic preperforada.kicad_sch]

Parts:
F1: Placa; PinSocket_1x02_P2.54mm_Vertical
GND1, GND2: GND; PinSocket_1x08_P2.54mm_Vertical
GND3: GND; PinHeader_1x04_P2.54mm_Vertical
M1: Motor 1; PinSocket_1x06_P2.54mm_Vertical
M2: Motor 2; PinSocket_1x06_P2.54mm_Vertical
P1: Fuente; PinSocket_1x02_P2.54mm_Vertical
PL1: Pistas logicas 1; PinSocket_1x08_P2.54mm_Vertical
PL2: Pistas logicas 2; PinSocket_1x08_P2.54mm_Vertical
RJ1, RJ2, RJ3, RJ4, RJ5, RJ6, RJ7, RJ8: RJ12; RJ12_Amphenol_54601
RRJ5: Rl12-6; PinHeader_1x06_P2.54mm_Vertical
RUT1: Enrrutador; PinHeader_1x11_P2.54mm_Vertical
Rrj6, Rrj7, Rrj8: Rl12-6; PinHeader_1x06_P2.54mm_Vertical
S1: Sosten; PinSocket_1x02_P2.54mm_Vertical
VCC1, VCC2: VCC; PinSocket_1x08_P2.54mm_Vertical
VCC3: VCC; PinHeader_1x04_P2.54mm_Vertical

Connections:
+3.3V: RJ1.1, RJ2.1, RJ3.1, VCC1.1, VCC1.2, VCC1.3, VCC1.4, VCC1.5, VCC1.6, VCC1.7, VCC1.8, VCC2.1, VCC2.2, VCC2.3, VCC2.4, VCC2.5, VCC2.6, VCC2.7, VCC2.8, VCC3.1, VCC3.2, VCC3.3, VCC3.4
GND: GND1.1, GND1.2, GND1.3, GND1.4, GND1.5, GND1.6, GND1.7, GND1.8, GND2.1, GND2.2, GND2.3, GND2.4, GND2.5, GND2.6, GND2.7, GND2.8, GND3.1, GND3.2, GND3.3, GND3.4, RJ1.3, RJ2.3, RJ3.3
unnamed: F1.1, P1.2
unnamed: F1.2, P1.1
unnamed: PL1.1, RUT1.9
unnamed: PL1.2, RUT1.10
unnamed: PL1.3, RUT1.11
unnamed: PL1.4, RJ4.6
unnamed: PL1.5, RJ4.1
unnamed: PL1.6, RJ3.5
unnamed: PL1.7, RJ2.5
unnamed: PL1.8, RJ1.5
unnamed: PL2.1, RUT1.1
unnamed: PL2.2, RUT1.2
unnamed: PL2.3, RUT1.3
unnamed: PL2.4, RUT1.4
unnamed: PL2.5, RUT1.5
unnamed: PL2.6, RUT1.6
unnamed: PL2.7, RUT1.7
unnamed: PL2.8, RUT1.8
unnamed: RJ5.1, RRJ5.1
unnamed: RJ5.2, RRJ5.2
unnamed: RJ5.3, RRJ5.3
unnamed: RJ5.4, RRJ5.4
unnamed: RJ5.5, RRJ5.5
unnamed: RJ5.6, RRJ5.6
unnamed: RJ6.1, Rrj6.1
unnamed: RJ6.2, Rrj6.2
unnamed: RJ6.3, Rrj6.3
unnamed: RJ6.4, Rrj6.4
unnamed: RJ6.5, Rrj6.5
unnamed: RJ6.6, Rrj6.6
unnamed: RJ7.1, Rrj7.1
unnamed: RJ7.2, Rrj7.2
unnamed: RJ7.3, Rrj7.3
unnamed: RJ7.4, Rrj7.4
unnamed: RJ7.5, Rrj7.5
unnamed: RJ7.6, Rrj7.6
unnamed: RJ8.1, Rrj8.1
unnamed: RJ8.2, Rrj8.2
unnamed: RJ8.3, Rrj8.3
unnamed: RJ8.4, Rrj8.4
unnamed: RJ8.5, Rrj8.5
unnamed: RJ8.6, Rrj8.6

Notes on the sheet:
Entradas de tension y masa
Coneccion con fuente externa
Coneccion logica
Servomotores

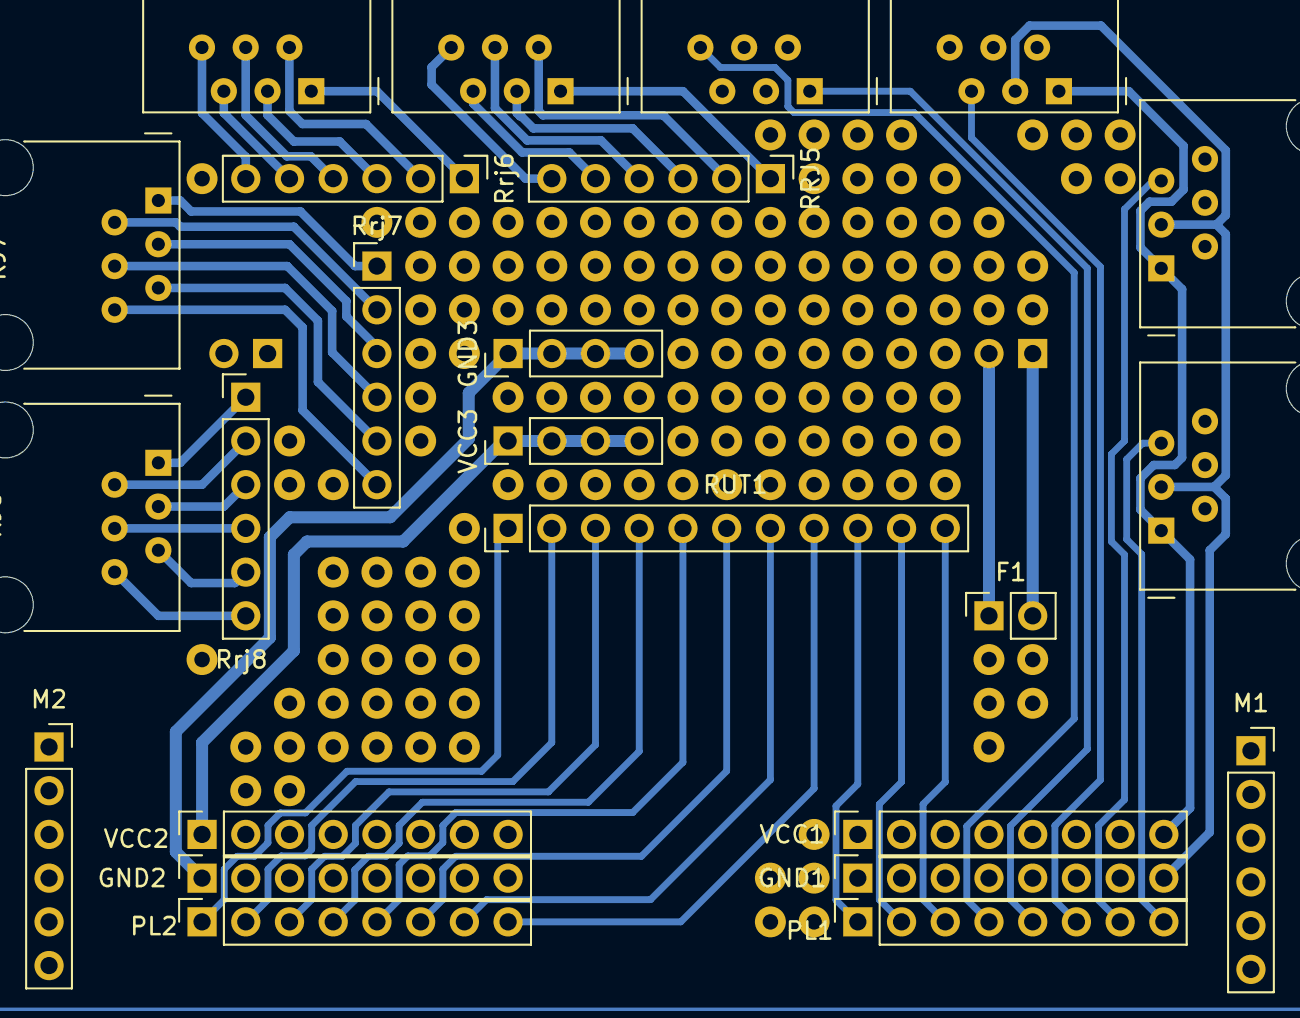
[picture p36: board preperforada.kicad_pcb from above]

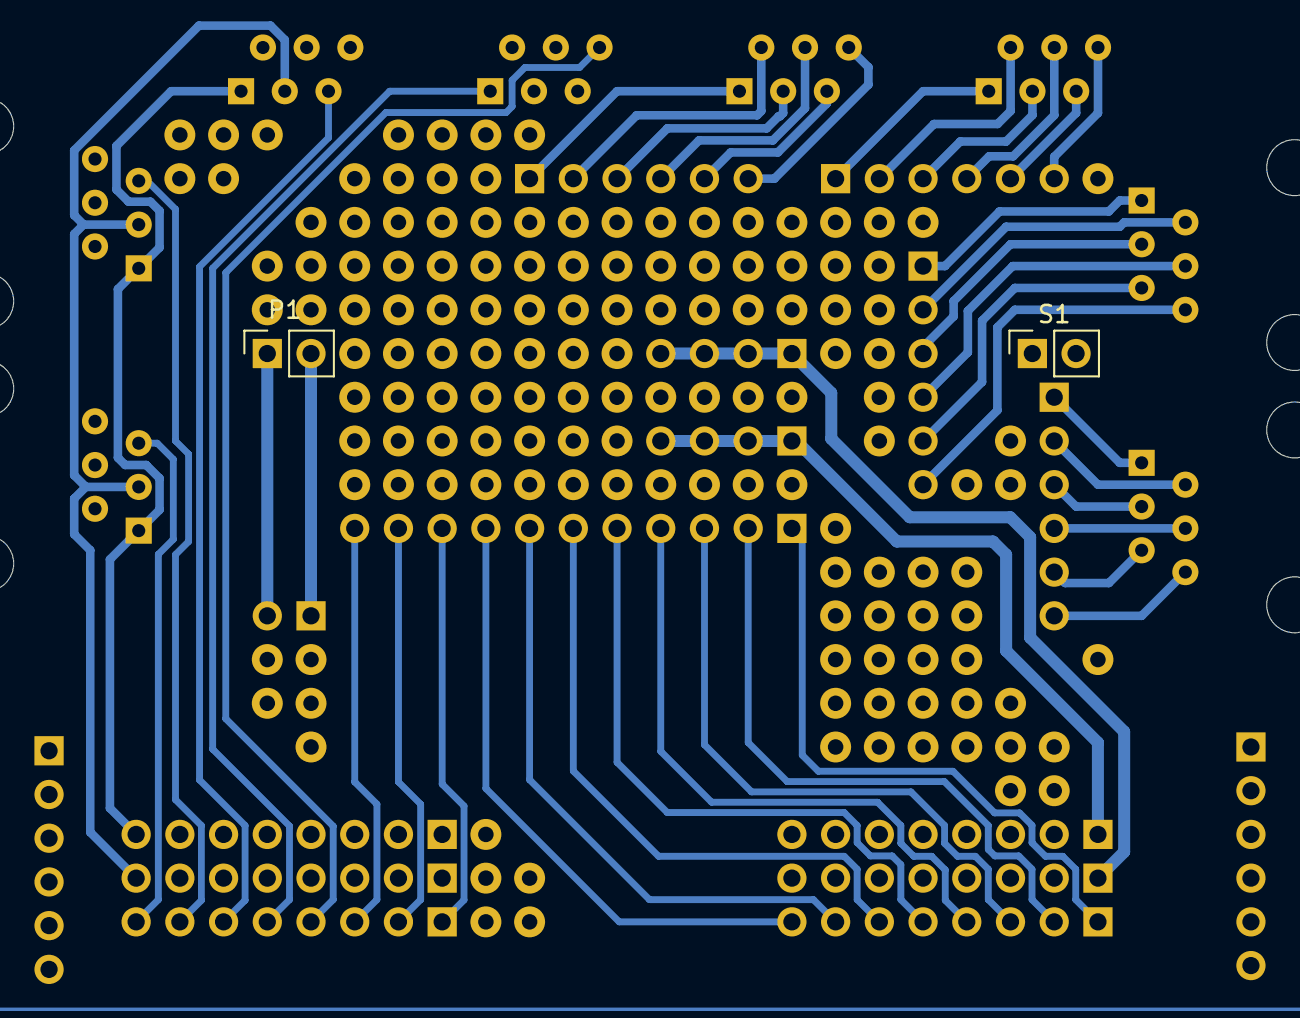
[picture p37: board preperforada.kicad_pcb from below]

Board: 2 copper layers, 26 parts (2 on the bottom side), 44 nets.

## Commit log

2026-04-02 inicial (cierre de 2.4.2.3)
    [gabinete.stl, preperforada.kicad_pcb, preperforada.kicad_sch]
2026-04-09 instrucciones de fabricación
